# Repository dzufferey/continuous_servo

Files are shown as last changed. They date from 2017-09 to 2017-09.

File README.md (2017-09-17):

# Continous Servo

## BoM

* [Teensy LC](https://www.pjrc.com/teensy/teensyLC.html)
* Electric motor with quadrature encoder ([pololu metal gearbox motor 25D with 48 CPR encoder](https://www.pololu.com/product/3239)) with mounting bracket ([Pololu 25D mm Metal Gearmotor Bracket Pair](https://www.pololu.com/product/2676))
* [MAX14870 Single Brushed DC Motor Driver Carrier](https://www.pololu.com/product/2961)
* Voltage regulator that output 5V ([Pololu Adjustable Step-Up/Step-Down Voltage Regulator S7V8A](https://www.pololu.com/product/2118))
* Through-hole resistors: 2 x 39kΩ, 2 x 68kΩ
* Electrolitic capacitors: ...
* 12V PSU with 5mm/2.1mm barrel jack
* female adapter for 5mm/2.1mm barrel jack
* headers and stuffs ...

## Attributions

* The Kicad modules for Teensy-LC was adapted from the code at https://github.com/hedrickbt/teensy_breakout by Brooke Hedrick released under MIT License.
* `resources/max14870.wrl` is derived from [MAX14870 Single Brushed DC Motor Driver Carrier model by Pololu](https://www.pololu.com/file/0J1338/max14870-single-brushed-dc-motor-driver-carrier.step), license unclear ...

## License

The content of this project itself (excluding attributed parts) is licensed under the Creative Commons Attribution 3.0 license, and the source code in the `motor_pid` folder is licensed under the MIT license.

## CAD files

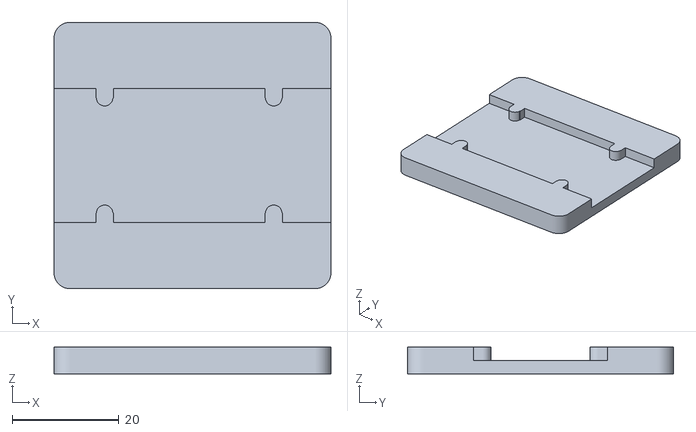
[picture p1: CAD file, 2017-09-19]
ready_to_make/models/motor_bracket_support.stl
52.0 x 50.0 x 5.00

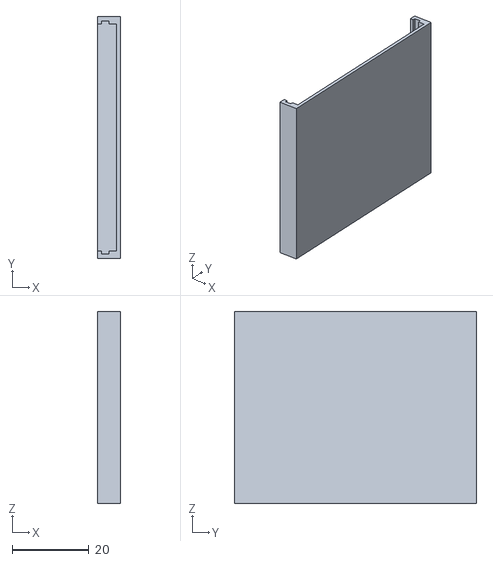
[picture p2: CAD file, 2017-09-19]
ready_to_make/models/pcb_support.stl
6.00 x 63.0 x 50.0

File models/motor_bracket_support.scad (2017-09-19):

$fn=60;

//to fit motor mounting bracket: https://www.pololu.com/file/download/2676-bracket-dimensions.pdf?file_id=0J825

tolerance = 0.1;
offsetX1 = 9.5;
offsetX2 = offsetX1 + 6.35 * 5 ;
offsetY1 = (25-21.7)/2;
offsetY2 = 25 - offsetY1;
d=3.3;
r=3.3/2 - tolerance;

module neg() {
    difference() {
        translate([0,-tolerance])square([52,25+2*tolerance]);
        translate([offsetX1,offsetY1-r]) square(d, true);
        translate([offsetX1,offsetY1]) circle(r);
        translate([offsetX2,offsetY1-r]) square(d, true);
        translate([offsetX2,offsetY1]) circle(r);
        translate([offsetX1,offsetY2+r]) square(d, true);
        translate([offsetX1,offsetY2]) circle(r);
        translate([offsetX2,offsetY2+r]) square(d, true);
        translate([offsetX2,offsetY2]) circle(r);
    }
}

difference() {
    minkowski() {
        translate([3,3,0]) cube([46,44,4]);
        cylinder(r=3,h=1);
    }
    translate([0,12.5,2.5]) linear_extrude(h=3) neg();
}

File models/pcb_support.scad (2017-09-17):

module support() {
    difference(){
        cube([50,63,6]);
        translate([2,2,1]) cube([50,59,5]);
        translate([1.2,1.2,3]) cube([50,60.6,2]);
    }
}

//rotate to print without overhang, but brim is advised
rotate([0,-90,0]) support();

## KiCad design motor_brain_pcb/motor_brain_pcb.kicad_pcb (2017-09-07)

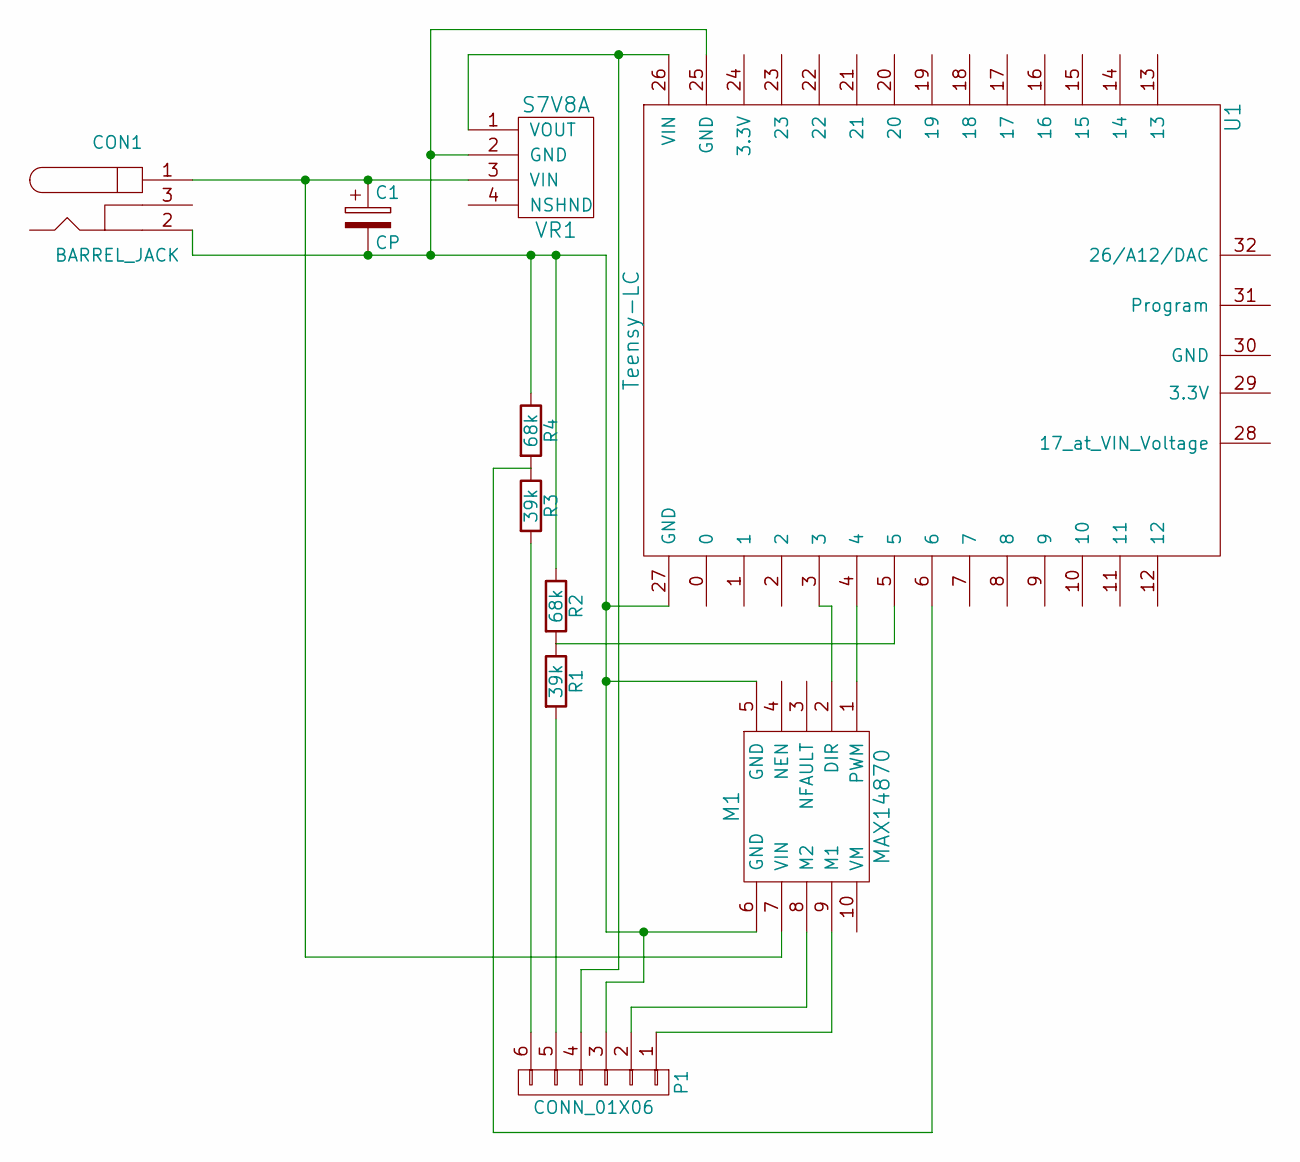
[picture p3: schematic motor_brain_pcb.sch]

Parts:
C1: CP; C_Radial_D10_L16_P5
CON1: BARREL_JACK
M1: MAX14870
P1: CONN_01X06; Socket_Strip_Straight_1x06
R1, R3: 39k; Resistor_Horizontal_RM10mm
R2, R4: 68k; Resistor_Horizontal_RM10mm
U1: Teensy-LC; teensy-lc
VR1: S7V8A

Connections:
unnamed: C1.1, CON1.1, M1.7 (VIN), VR1.3 (VIN)
unnamed: C1.2, CON1.2, M1.5 (GND), M1.6 (GND), P1.3, R2.1, R4.1, U1.25 (GND), U1.27 (GND), VR1.2 (GND)
unnamed: M1.1 (PWM), U1.4
unnamed: M1.2 (DIR), U1.3
unnamed: M1.8 (M2), P1.2
unnamed: M1.9 (M1), P1.1
unnamed: P1.4, U1.26 (VIN), VR1.1 (VOUT)
unnamed: P1.5, R1.2
unnamed: P1.6, R3.2
unnamed: R1.1, R2.2, U1.5
unnamed: R3.1, R4.2, U1.6

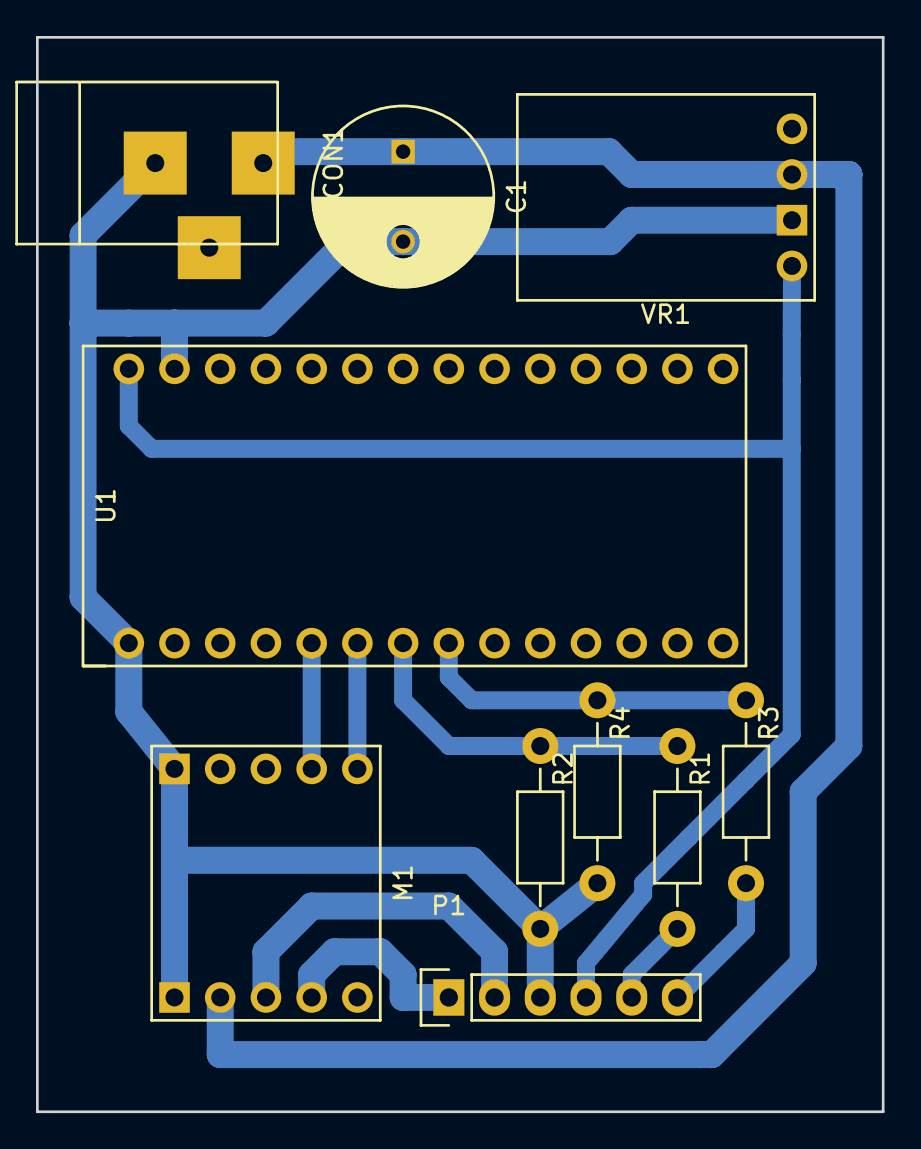
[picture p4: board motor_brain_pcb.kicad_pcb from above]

Board: 2 copper layers, 47.0 x 59.7 mm, 10 parts (0 on the bottom side), 11 nets.

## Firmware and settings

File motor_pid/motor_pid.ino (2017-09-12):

//dealing with the input
//  type of control:
//      set speed
//      [optional] set position
//  USB communication / Serial: https://www.pjrc.com/teensy/td_serial.html

// voltage divider with 39k and 68k

//implement a PID controller (periodic loop)
//  it runs within interrupt so it better be fast!
//  sources:
//    http://controlsystemslab.com/discrete-time-pid-controller-implementation/
//    http://brettbeauregard.com/blog/2011/04/improving-the-beginners-pid-introduction/
//    https://github.com/br3ttb/Arduino-PID-Library/
//    http://playground.arduino.cc/Code/PIDLibrary

//TODO when switching direction, should we stay in break mode for a little while ?

//motor encoder
//  counts
//      20.4:1 gearbox -> 979.62 counts per revolution
//      46.85:1 gearbox -> 2248.86 counts per revolution
//  https://www.pjrc.com/teensy/td_libs_Encoder.html
//  interupts pin:
//      Teensy 3.5  all but not 13
//      Teensy LC   2 - 12, 14, 15, 20 - 23
//  does the interrupt on time and interrupt on the input pins affect each-other? If not, the encoder can use a more optimized code.
//      the code of IntervalTimer look like it does not use attachInterrupt...

//controling the motor driver:
//  motor driver freq up to 50 kHz: https://www.pololu.com/file/download/MAX14870.pdf?file_id=0J885
//  https://www.pjrc.com/teensy/td_pulse.html
//  Teensy LC pins: FTM0    6, 9, 10, 20, 22, 23            488.28 Hz
//                  FTM1    16, 17                          488.28 Hz
//                  FTM2    3, 4                            488.28 Hz
//  set the frequency: analogWriteFrequency(4, 375000); // Teensy pin 3 also changes to 375 kHz
//  set the number of bits for analogWrite: analogWriteResolution(12);  // analogWrite value 0 to 4095, or 4096 for high
//  frequency and resolution goes together:
//    LC: 10 bits, 46'875 Hz

// #define ENCODER_OPTIMIZE_INTERRUPTS
#include <Encoder.h>
#include <IntervalTimer.h>

// Code for a Teensy LC

// TODO should this be a power of 2 to make the computation is simpler?
#define PID_USEC 1000

// Motor parameter
#define CNT_PER_REV 979.62 //20.4:1 gearbox
//#define CNT_PER_REV 2248.86 //46.85:1 gearbox

const int LED_PIN = 13;
const int ENCODER_PIN_1 = 5;
const int ENCODER_PIN_2 = 6;
const int DIR_PIN = 3;
const int PWM_PIN = 4;
const int PWM_BITS = 10;
const int PWM_FREQ = 46875;

const int MAX_PWM = 1 << PWM_BITS;

const char EOL = '\n';

const bool SPEED = true;
const bool POSITION = false;

const int KP_SPEED = 20;
const int KI_SPEED = 2000;
const int KD_SPEED = 100;

const int KP_POSITION = 56;
const int KI_POSITION = 500;
const int KD_POSITION = 500;

Encoder motor_encoder(ENCODER_PIN_1, ENCODER_PIN_2); 

IntervalTimer pid_tick;

// PID parameters, volatile because the UI code might change it
volatile int KP = 0;
volatile int KI = 0;
volatile int KD = 0;

//PID state variable
volatile bool mode = SPEED;
volatile float target = 0; //written by `loop`, read by `pid`
volatile float current = 0; //written by `pid`, read by `loop`
float i = 0;
// keep the previous output to limit the jerk
int pid_output = 0;
//to synchronize between context
unsigned int loop_count = 0;
volatile unsigned int w1 = 0;
volatile unsigned int w2 = 0;

// Amortize the number of counts over a window.
// This increases the precision at low speed and implements a low pass filter.
// But is also adds some lag
const int window = 24;
int counts[window];
int count = 0;
int idx = 0;

//TODO min/max range for the speed

void pid_loop(void) {
    loop_count += 1;
    w1 = loop_count; // start writing stuff
    // read the motor state (wired backward ...)
    int ticks = -motor_encoder.read();
    motor_encoder.write(0);
    count -= counts[idx];
    counts[idx] = ticks;
    count += ticks;
    idx += 1;
    if (idx >= window) {
      idx = 0;
    }
    // update the PID state
    float new_state;
    if (mode == SPEED) {
        new_state = ((float)count) / ((float)window);
    } else {
        new_state = current + ticks;
    }
    float p0 = target - new_state;
    float p = KP * p0;
    float d = KD * (current - new_state);
    int pd = (int)(p + d);
    pd = max(-MAX_PWM, pd);
    pd = min( MAX_PWM, pd);
    i = i + KI * p0 * PID_USEC / 1000000;
    // clamp the integral term when the PID is outside the range of output
    if (pd >= 0) {
        i = min( MAX_PWM -pd, i);
    } else {
        i = max(-MAX_PWM -pd, i);
    }
    int pid = pd + (int)i;
    //TODO limit the jerk
    // set the output
    if (pid >= 0) {
        if (pid_output < 0) {
            digitalWrite(DIR_PIN, HIGH);
        }
        analogWrite(PWM_PIN, pid);
    } else {
        if (pid_output >= 0) {
            digitalWrite(DIR_PIN, LOW);
        }
        analogWrite(PWM_PIN, -pid);
    }
    // save the state
    current = new_state;
    pid_output = pid;
    w2 = loop_count; // done writing stuff
}


void output() {
    int _w1 = w1;
    int _pid_output = pid_output;
    int _i = i;
    float _current = current;
    int _w2 = w2;
    if (_w1 == _w2) {
        if (mode == SPEED) {
            Serial.print("speed, ");
        } else {
            Serial.print("position, ");
        }
        Serial.print("target = ");
        Serial.print(target);
        Serial.print(", current = ");
        Serial.print(_current);
        Serial.print(", output = ");
        Serial.print(_pid_output);
        Serial.print(", i = ");
        Serial.print(_i);
        Serial.print(", w = ");
        Serial.println(_w1);
    } //else: we were interrupted, skip
}

void set_mode(bool m) {
    // make sure the PID is stopped
    pid_tick.end();
    // stop the motor
    digitalWrite(DIR_PIN, HIGH);
    analogWrite(PWM_PIN, 0);
    // clean the values
    target = 0;
    current = 0;
    mode = m;
    for (int i = 0; i < window; i++) {
        counts[i] = 0;
    }
    count = 0;
    idx = 0;
    // set the new coefficients
    if (m == SPEED) {
        KP = KP_SPEED;
        KI = KI_SPEED;
        KD = KD_SPEED;
    } else {
        KP = KP_POSITION;
        KI = KI_POSITION;
        KD = KD_POSITION;
    }
    // (re)start the PID
    pid_tick.begin(pid_loop, PID_USEC);
}

void read_input() {
    digitalWrite(LED_PIN, HIGH);
    // read the input: change mode, speed in turn per second, or position in turn
    String input = Serial.readStringUntil(EOL);
    //Serial.print("cmd = ");
    //Serial.println(input);
    if (input.length() > 0) {
        if (input[0] == 'p' || input[0] == 'P') {
            set_mode(POSITION);
        } else if (input[0] == 's' || input[0] == 'S') {
            set_mode(SPEED);
        } else {
            //float input = Serial.parseFloat();
            float f = input.toFloat();
            if (mode == SPEED) {
                // convert the speed to count per PID loop
                target = f * CNT_PER_REV * PID_USEC / 1000000;
            } else {
                // convert the position to a count
                // round to avoid oscillations
                target = (int)(f * CNT_PER_REV);
            }
        }
    }
    // flush the remaining input
    while (Serial.available() > 0) {
        Serial.read();
    }
    digitalWrite(LED_PIN, LOW);
}

// Arduino functions

void setup() {
    pinMode(DIR_PIN, OUTPUT);
    pinMode(PWM_PIN, OUTPUT);
    pinMode(LED_PIN, OUTPUT);
    
    analogWriteFrequency(PWM_PIN, PWM_FREQ);
    analogWriteResolution(PWM_BITS);
    
    Serial.begin(9600);

    set_mode(SPEED); //set_mode also start the PID loop
}

void loop() {
    if (Serial.available()) {
        read_input();
    }
    delay(100);
    output();
}

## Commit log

2017-09-04 1st draft
    [motor_brain_pcb.kicad_pcb, motor_brain_pcb.sch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]
2017-09-07 code: control speed or position
    [motor_brain_pcb.kicad_pcb]
2017-09-12 wired the encoder backward
2017-09-12 tuning PID
2017-09-17 adding some models and info
    [motor_bracket_support.scad, pcb_support.scad]
2017-09-19 output files to new folder
    [motor_bracket_support.scad, motor_bracket_support.stl, pcb_support.stl]
